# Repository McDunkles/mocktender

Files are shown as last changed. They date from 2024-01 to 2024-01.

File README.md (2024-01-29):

# L3-G8 Mocktail Mixing Machine Project

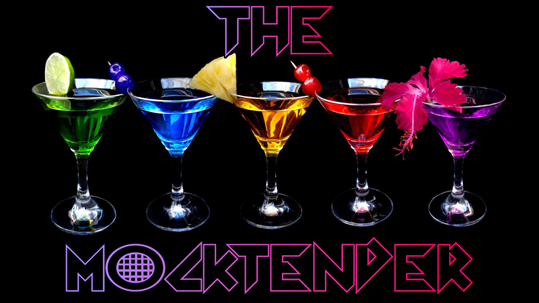
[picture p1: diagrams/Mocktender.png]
Mocktender Title Image


## Team Members:
The Mocktender was developped in Winter 2023 for the SYSC 3010 class by:
- Matt Reid
- Ethan Bradley
- Duncan MacLeod

#### TA: Roger Selzler

## About the Project
A mocktail is a non-alcoholic drink that captures the essence of a cocktail without the downsides of alcohol consumption. From work offices where you want to stay sharp while having fun drinks for lunch to wanting a healthier alternative to drinking cocktails at home. To provide the ease of having drinks at home or private events without needing to buy equipment and learn how to mix them yourself or paying a bartender, the Mocktender will provide the ability to create mocktails at home with ease. 

The Mocktender provides a web interface GUI that can be used to remotely view liquid levels, add recipes, change settings, and dispense drinks. Our project has three raspberry pi devices, one for the user interface, one for the machine (IOController), and one to simulate a second machine. The machine itself has a Raspberry Pi control device which is connected by GPIO to ultrasonic sensors to get the liquid level in real time. When a recipe is specified, it is sent through a Firebase real time database to the control device which runs peristaltic pumps to dispense the drink. An LCD displays output to the user of the machine showing the status of the machine.

## Contents
The contents of the top level directories are as follows:
- [/src](/src): Source code for the Mocktender including tests
- [/diagrams](/diagrams): Diagrams/Images used in Mocktender documentation and reports
- [/WIPUR](/WIPUR): Weekly Individual Projecet Update Reports
- [/3D_models](/3D_modles): 3D models for the liquid pump system (not used in final version)
- [/schematics](/schematics): Schematics used in Mocktender documentation and reports

The SRC (source code) folder contains the following directories:
- [/src/IOController](/src/IOController): Code for the IOController node which represents the real Mocktender machine
- [/src/SystemSimulator](/src/SystemSimulator): Code for the SystemSimulator node which simulates a Mocktender machine
- [/src/UserInterface/mkt-ui](/src/UserInterface/mkt-ui): Code for the UserInterface node which runs the Web Interface
- [/src/mkt-persistance](/src/mkt-persistane): Code for the persistance layer of the UserInterface node
- [/src/end2end](/src/end2end): Code and testing plan for the end to end test demonstration
- [/src/unittest](/src/unittest): Unit tests for the Mocktender machine. Includes the unit testing demo plan

## Installation
### Hardware

#### Electronics Necessary 
To build the hardware components of a Mocktender, the following components will be required:
- 1x Raspberry Pi 4B
- 3x UltraSonic Sensor
- 3x Peristaltic Pumps
- 2x L298N Dual H-Bridge driver
- 1x 1602A LCD Module
- 4x 220Ω resistor
- 3x 330Ω resistor
- 1x 2.2KΩ resistor
- 2x 9V rechargeable batteries

For documentation on how to connect these components together, please refer to Section 4 of the [Detailed Design Document](/documents/SYSC3010-TheMocktenderDetailedDesign-L3G8.pdf)

Food grade silicone hosing will also be required for pumping the liquid from the internal containers to a choice of reservoir.

### Software
#### Dependencies
A number of libraries need to be installed for a Mocktender to work.
The following commands can be used to install the necessary libraries (You may have to use `sudo` to install these properly):

```
python3 -m pip install pyrebase
python3 -m pip install gpiozero
python3 -m pip install adafruit-circuitpython-charlcd
```

#### Firebase Configuration
To begin getting the software all setup for a Mocktender, a Firebase Real-Time Database would need to be created for the user. The credentials for the project need to be filled out in [MocktenderConfig.py](/src/IOController/MocktenderConfig.py) as can be seen below:

```python
CONFIG_PROD = {
        "apiKey": "your-firebase-project-api-key",
        "authDomain": "your-firebase-project.firebaseapp.com",
        "databaseURL": "https://your-firebase-project-rtdb.firebaseio.com/",
        "storageBucket": "your-firebase-project.appspot.com"
}
```
In [dbFormat.json](/src/IOController/dbFormat.json), fill out the id value to be a name of your choosing.

```json
{
	"id": "device id name"
}
```
At the root of the project repo, the user should run the following commands

```bash
cd src/IOController/
python3 MocktenderRegistration.py production
```

This will upload the necessary schema to the Firebase Real-Time Database to run the Mocktender.

#### Email Notification Configuration 
The Mocktender also has email notification sending capabilities. To be able to use this functionality properly, please refer to [this repository](https://github.com/Brethan/ipy-mailer) for detailed instructions on how to set up an email for SMTP purposes.

In [notif_config.json](src/IOController/mailer/notif_config.json), use the values from the aforementioned instructions and paste them in this file.

```json
{
	"app_pw": "app-password",
	"sender": "your-python-smtp-email@gmail.com",
	"sender_name": "Mocktender"
}
```
## Usage
#### IOController Deployment
The IOController of the Mocktender can now be deployed by running the following commands at the root of the project directory:
```bash
cd src/IOController/
python3 IOLiquidLevel.py & python3 IOController.py production &
```

You should see IO device related errors due to IOLiquidLevel.py, followed by decimal numbers which are the 
measured liquid levels from the UltraSonic sensors. If one is paying attention to the Firebase RTDB,
they will noticed that there will be timestamped liquid levels being added to it.

Additionally, there will be errors from IOController.py due to issues with the asyncio API. The LCD screen
should say "Mocktender Ready" once it has been initialized.

The errors will not affect the runtime of the Mocktender.
## The Mocktender Machine
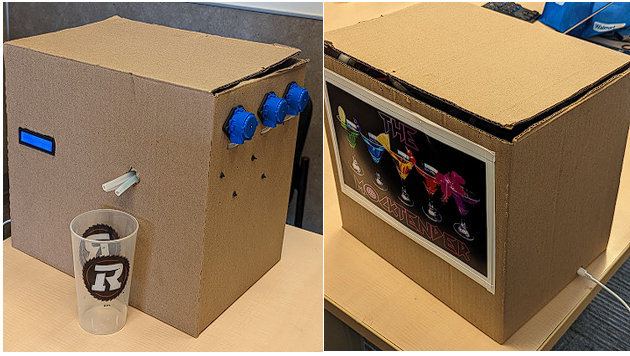
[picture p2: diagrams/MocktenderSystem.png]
Mocktender Machine


## UML Deployment Diagram

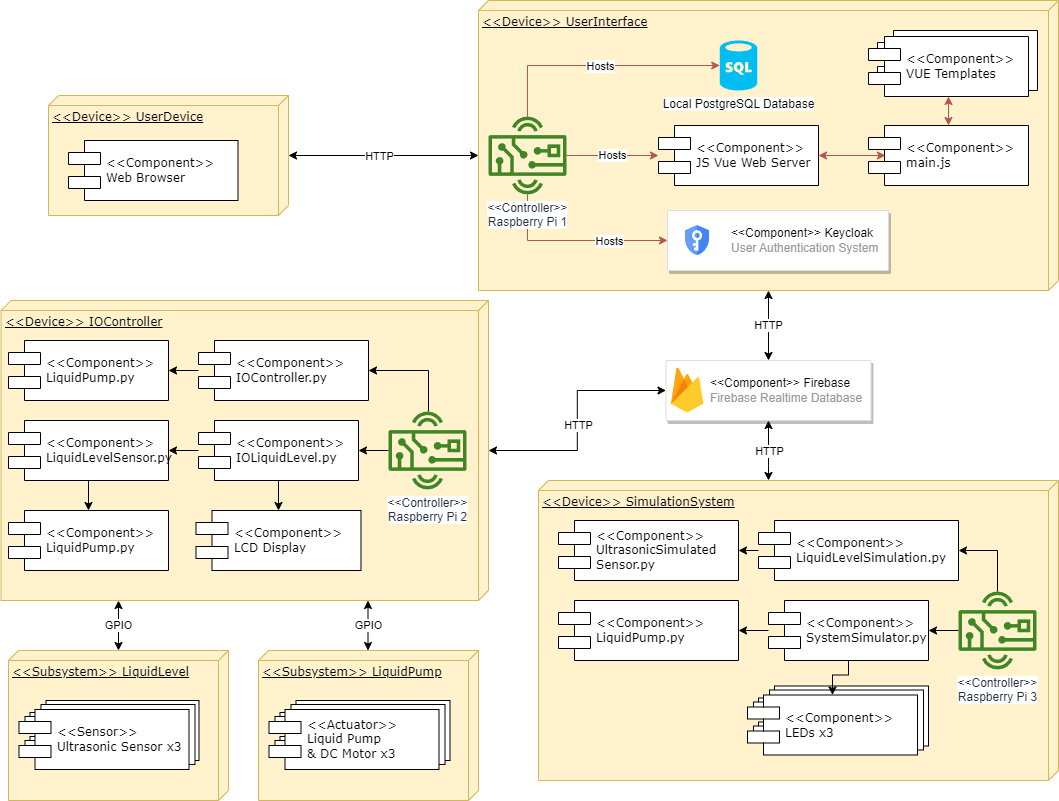
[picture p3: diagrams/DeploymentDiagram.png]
UML Deployment Diagram


## Project Milestones

| Milestone # | Name | Description |
| ---| -----| --- |
| 1 | Uploading and Fetching Data | Computer devices can read from and write data to a real-time database independently of each other, which can then be accessed and displayed on an external device. |
| 2 | Communication Between Nodes | Communication established between computer devices (HTTP etc.) to transfer data stored locally between nodes and issue commands. |
| 3 | Measurement and Conditional Actuation | Liquid level of a fixed container can be measured accurately using sensors can uploaded to the database. Data can be used to turn on an LED when a threshold is reached. |
| 4 | Exposing Data to the World | Two additional containers with liquid level measuring will also have their data uploaded to the database. The liquid level will be displayed as text on a webserver |
| 5 | Hardware Assembly | Assembled liquid dispensing system utilizing peristaltic pumps. Liquid level on webserver should be updated (as text) in real-time. |
| 6 | Graphical User Interface | Webserver displays the volume of the liquid containers as an animation. Users can navigate between different webpages on the server. |
| 7 | Controlling the Hardware System with UI | Webserver component can control all 3 liquid pumps implementing the drink mixing. Users can login and save customs mixtures locally and in the real-time database. |

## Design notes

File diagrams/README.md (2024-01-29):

# Mocktender Diagrams

Folder containing diagrams (deployment, class, and sequence) used for Mocktender documentation and reports

## Deployment Diagram
Deployment Diagram

## Sequence Diagrams
### CheckLiquidLevels Use Case
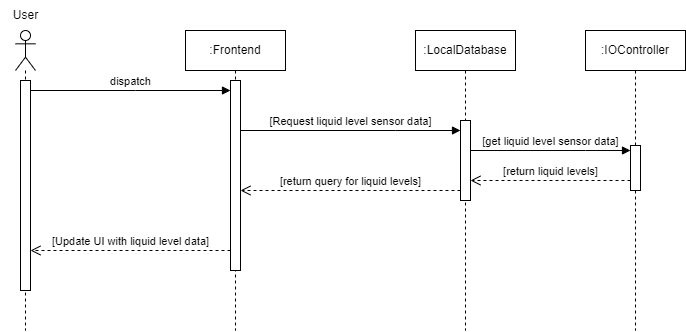
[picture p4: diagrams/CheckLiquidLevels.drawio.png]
CheckLiquidLevels


### MakeDrink Use Case
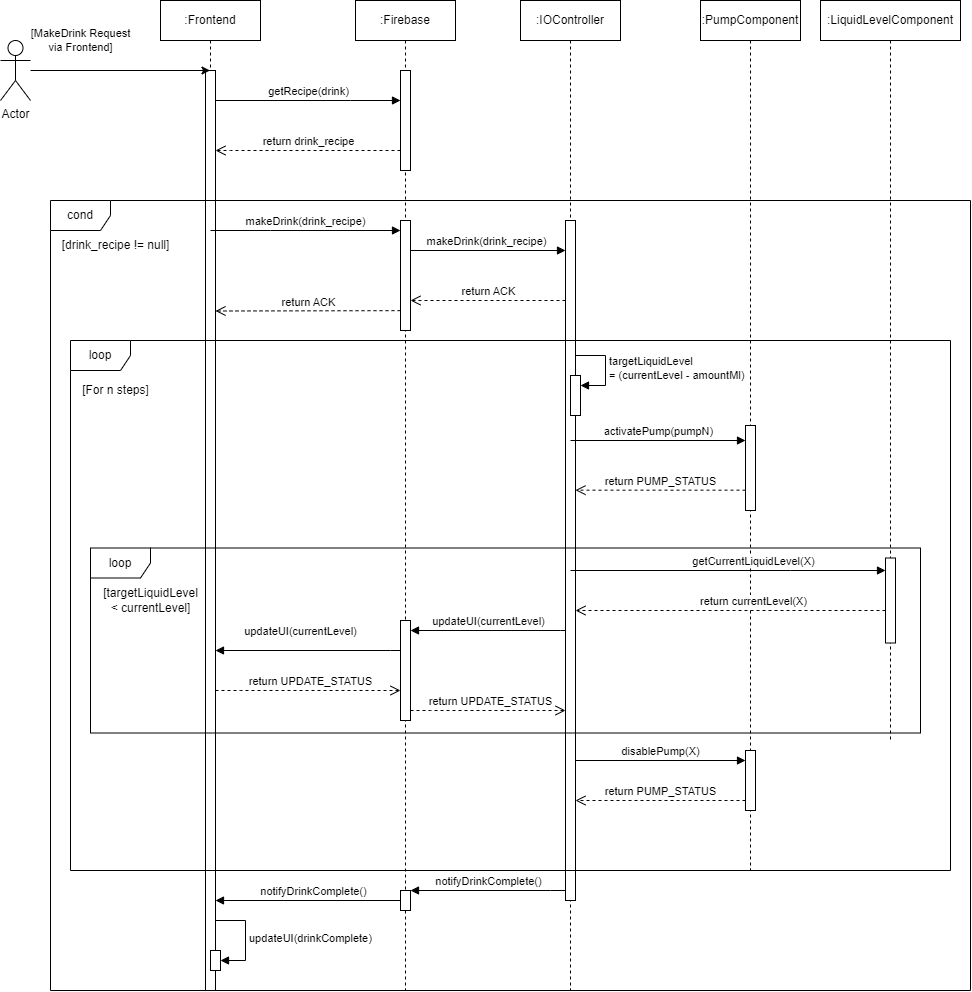
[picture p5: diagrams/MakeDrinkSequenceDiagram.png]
MakeDrink


## Class Diagrams
### IOController
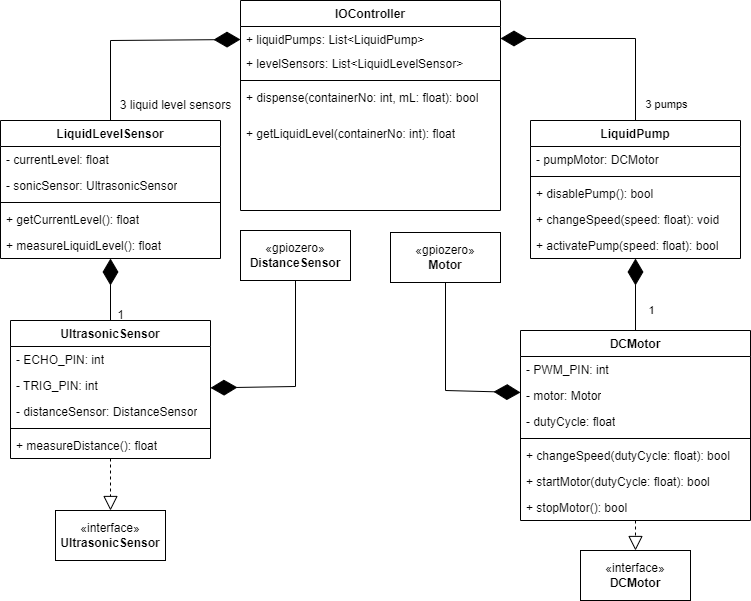
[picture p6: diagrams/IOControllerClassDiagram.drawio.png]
IOController


### IOSimulator
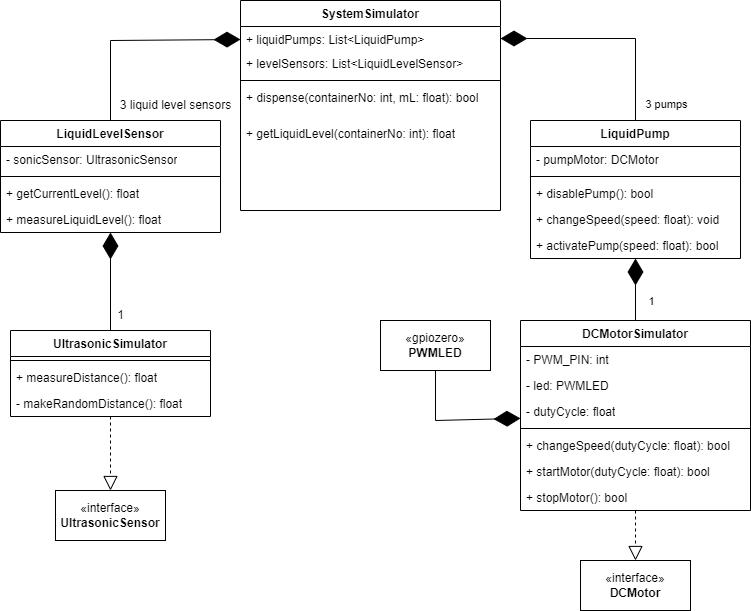
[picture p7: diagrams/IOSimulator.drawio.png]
IOSimulator


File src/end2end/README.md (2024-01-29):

# L3-G8 End-to-End Testing Demonstration
### Completed on March 10th, 2023

## Testing Plan
The Mocktender machine consists of multiple Raspberry Pi devices that need to communicate amongst each other to meet our project goals. The system is distributed between the Pi devices with one device hosting the front-end web interface for viewing the state of the machine and controlling the hardware devices. The User Interface device is responsible for updating the Firebase database with the liquid level sensor data and sending the signals to the hardware devices. The Sensor System and Simulation devices perform the same communication, so only one of them needs to be tested in end-to-end testing.
     To test the end-to-end communication between the components, all the messages discussed in Section 2.1 will need to be created. The test scripts created will generate the messages, send them to the correct end destination, and the end destination will confirm that the message was received, and the contents are as expected. The test will pass if the message is the same as was expected, and will fail if either no message was received, or the contents are different than was expected. To provide test feedback, the messages will be printed to a console that will also be available on the Raspberry Pi devices whenever needed as a debugging option. The database contents on the Firebase real time database will also be tested after the messages are sent to ensure that the contents are as expected.

The following steps will be performed in our end-to-end testing demonstration:
1. First, the connections between the Raspberry Pi devices, and the Firebase real time database will be tested. A test script will verify that all of the Pi devices are able to connect to the Firebase server.
2. Next, messages will be sent between Pi devices over the Firebase database to demonstrate that messages can be sent and received through that database.
3. Finally, a Flask web server will be created to demonstrate that a button press can send a message from the user interface pi to the Firebase database.

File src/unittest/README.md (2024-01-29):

# Mocktender Unit Testing Demo
### Group number: L3-G8

To test that each individual hardware and software component works as expected, the following hardware and software unit tests will be performed. A copy of the deployment diagram showcasing the system under test is below:
UML Deployment Diagram

## Hardware Unit Testing
| **Hardware Device** | **Tester** | **Device Description** | **Test Description** | **Expected Test** **Results** |
| --- | --- | --- | --- | --- |
| **Ultrasonic Sensor (Liquid level sensing)** | Matt | The ultrasonic sensor will be used to track the water level in the 3 liquid tanks in the Mocktender system. The distance from the sensor to the surface of the water is used to calculate the current volume of the liquid in the container. | To test the liquid level system is working correct, water will be added to the liquid container in increments of 2cm measured using a ruler. The Ultrasonic sensor will measure the distance to the surface of the water | The distance from the sensor to the surface of the water should  be within 5mm of the expected level based on the amount of water added to the container. |
| **Peristaltic Pump & DC Motor** | Ethan | The liquid pump will be used to dispense a drink. Based on the recipe provided by the user, each pump will be run for a specified amount of time so that the correct amount of each liquid is pumped (mixed) into the dispensed drink. | To test the functionality of the pump, the GPIO pin connected to the motor controller will be pulsed with PWM signals. The amount of liquid that is pumped over a time period will be measured. | The pump will pump water for 30 seconds in each trial, and approximately 50mL should be pumped into the measurement contzainer. |
| **LCD Display** | Duncan | The LCD display will display machine operation information such as what it is dispensing and any errors. | To test the LCD output, messages will be displayed on the LCD. | The LCD display should display the correct messages. |
| **Simulation LEDs** | Duncan | The simulation LEDs will light up when the motors on the simulation device are ON. Based on the recipe provided by the user, each LED will turn on for a specified amount of time so that it can be demonstrated that the simulation is working as expected. | To test that the Simulation LEDs accurately turn ON when the motors should be running, the LEDs will be pulsed with PWM similarly to the Peristaltic Pump & DC Motor test. This is since the simulation LEDs are simulating the pump and motor system | Like the pump and motor test, the user should see the LEDs gradually get brighter as the PWM is increased until they reach their max brightness. They will maintain the maximum brightness for 2 seconds before gradually slowing down until they are OFF. |

## Software Unit Testing
| **Software** | **Tester** | **Software Description** | **Test Description** | **Expected Test Results** |
| --- | --- | --- | --- | --- |
| **Liquid Level Monitoring System** | Matt | The liquid level monitoring system will take the sensor data and calculate the volume of liquid currently in the container in real time. It sends this information to the user interface to display to the user. | To test the conversion from distance to liquid level, increments of distances of 0.1 will be converted to a volume and rounded to the nearest volume amount in the software. There will also be tests for error values (negative and too high) | The volume that the software returns should be equal to the expected closest multiple of 80 to the distance. If the distance is negative or bigger than the maximum size (640mL), it should give a volume of -1. |
| **Motor Control System** | Ethan | The motor control system takes the amount of liquid needed for the selected recipe and converts it into the time that the motor needs to run based on the calculated flow rate. | To test that the motor control system can convert the recipe into the correct times for each pump to pump the specified amount of liquid. | The time that the system “turns on the motor” should match the expected time based on the recipe and flow rate. |
| **Frontend Web Interface** | Duncan | The frontend web interface allows a user to view liquid levels, create recipes, and dispense a drink. It also allows an admin login to give administrative access to locking a machine and | The interface will be tested by rendering GUI design pages and ensuring that they render and display information as expected. | When a button is pressed, it should redirect to the correct page and display the expected info. |
| **Local PostgreSQL Database** | Duncan | The local SQLite database is used to store machine specific data for display on the web interface. | The database will be tested using a test script which creates the expected tables for the local system database. | The data stored in the PostgreSQL database after the script is run will be pulled and compared with the expected contents of the database. |

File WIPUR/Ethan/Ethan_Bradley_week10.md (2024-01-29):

## Weekly Individual Project Update Report
### Group number: L3-G8
### Student name: Ethan Bradley (101158848)

### Week 10 (March 22nd - 28th)
___
1. **How many hours did you spend on the project this week?** 21

2. **Give rough breakdown of hours:**
   1. Writing technical memo: writing 1 hour
   2. Peristaltic Pump redesign + troubleshooting: CAD 12 hours
   3. Fixing the gearbox for the pump: CAD 5 hours
   4. Connecting gearbox, pump, and motor controller together: wiring 2 hours
   5. Met with team to discuss the video: meeting 1 hour
   6. Buying 3 peristaltic pumps from Amazon: resignation 0 hours

3. ***What did you accomplish this week?***
   - Lowered the scale of technical memo to just using a slicer.
   - Finished the integration of the pump with the gearbox.
   - Gave up on 3D printing the pump and gearbox.
   - Met with team to discuss the project video
  
4. ***How do you feel about your progress?***
   - Good progress this week. Feel deflated about the pumps, but I'm getting more sleep so that's nice.

5. ***What are you planning to do next week***? 
   1. Work on the project video for next weeks class.
   2. Get the Amazon pumps working with the liquid pump source code.
   3. Model mounting brackets for the pumps and funnel.

6. ***Is anything blocking you that you need from others?*** 
   - Nothing is blocking me right now.

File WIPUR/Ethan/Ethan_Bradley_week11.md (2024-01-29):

## Weekly Individual Project Update Report
### Group number: L3-G8
### Student name: Ethan Bradley (101158848)

### Week 11 (March 29th - April 4th)
___
1. **How many hours did you spend on the project this week?** 30

2. **Give rough breakdown of hours:**
   1. Integration of Frontend and IOController of the Mocktender: 11 hours
   2. Hardware assembly of the Mocktender Machine and wiring: 9 hours
   3. Recording for the final project video: 6 hours
   4. Editing the final project video: 4 hours

3. ***What did you accomplish this week?***
   - Integration between Frontend and IOController is complete (Frontend can actuate pumps)
   - IOController feedback loop is in progress (Pumps pump liquid, and use ultrasonic level sensors as a correction factor)
  
4. ***How do you feel about your progress?***
   - Significant progress made this week, not much left to go for the final demo

5. ***What are you planning to do next week***? 
   1. Clean up the communication between different systems clean up repo
   2. Mount funnel properly for final demo

6. ***Is anything blocking you that you need from others?*** 
   - Nothing is blocking me right now.

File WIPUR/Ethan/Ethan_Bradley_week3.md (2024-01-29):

## Weekly Individual Project Update Report
### Group number: L3-G8
### Student name: Ethan Bradley (101158848)

### Week 3 (January 25th - 31st)
___
1. **How many hours did you spend on the project this week?** 4

2. **Give rough breakdown of hours spent on 1-3 of the following:**
   1. Discussing project idea and implementation with group members, 2 hours
   2. Researching mechanisms for fluid transfer, 2 hours
3. ***What did you accomplish this week?***
  - Group decided on a Mocktail machine for our project
  - Progess made on the draft project proposal
  - Discussed the structure of the of the machine
4. ***How do you feel about your progress?***
  - I am personally a bit behind, but catching up
5. ***What are you planning to do next week***? 
  - Full project proposal 
  - Draft CAD drawing for a peristaltic pump
  - Discuss budget for items required for project
6. ***Is anything blocking you that you need from others?*** 
  - Nothing is currently blocking me

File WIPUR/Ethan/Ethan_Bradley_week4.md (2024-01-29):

## Weekly Individual Project Update Report
### Group number: L3-G8
### Student name: Ethan Bradley (101158848)

### Week 4 (February 1st - 7th)
___
1. **How many hours did you spend on the project this week?** 6

2. **Give rough breakdown of hours spent on 1-3 of the following:**
   1. Creating the circuit diagrams for the Draft proposal - 2 hours.
   2. Writing allocated section for draft proposal - 3 hours
   3. Discussion with group members about the various design and implementation details for the Mocktender - 1 hour
      1. Note: Some of these events over lap
3. ***What did you accomplish this week?***
  - Implementation for liquid transfer for the Mocktender was discussed, was decided to use gravity and valves instead of pumps.
  - Draft project proposal has been completed
    - By extension, decided on communication protocol between computer devices, as well as the sensors used for the project
4. ***How do you feel about your progress?***
  - I am still behind on labs, however should be done by Wednesday night.
5. ***What are you planning to do next week***? 
  - Polishing up the final project proposal based on the peer review for the draft.
  - Research valve designs that can utilize (servo) motors instead of typical metal valves
  - Figure out which components can be ordered on digikey and submit order form.
  - Start playing around with components I have on hand that relate to our project (LCD screen, ultrasonic sensor, etc.)
6. ***Is anything blocking you that you need from others?*** 
  - Need Duncan to assign an issue on GitHub for lab 4.

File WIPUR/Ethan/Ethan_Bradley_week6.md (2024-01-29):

## Weekly Individual Project Update Report
### Group number: L3-G8
### Student name: Ethan Bradley (101158848)

### Week 7 (February 22nd - 28th)
___
1. **How many hours did you spend on the project this week?** 6

2. **Give rough breakdown of hours:**
   1. Scouting out construction materials for the frame of the mocktender: 1.5 hours
   2. Began working on the detailed design document: writing 2.5 hours
   3. Researched PCB design technologies and how to use them: research 2 hours

3. ***What did you accomplish this week?***
   - Group began work on the detailed design document
   - Contacted SCE services to book an appointment for soldering training.
  
4. ***How do you feel about your progress?***
   - A bit worried, we were hoping to get more done during reading week but we were not really able to find any time to work on the project specifically.

5. ***What are you planning to do next week***? 
   1. Need to get everything necessary prepared to work on the detailed design document.
   2. Getting training from SCE services to be able to use the soldering iron in the maker lab.
   3. Find suitable and affordable chassis for the Mocktender.

6. ***Is anything blocking you that you need from others?*** 
   - Nothing is blocking me right now.

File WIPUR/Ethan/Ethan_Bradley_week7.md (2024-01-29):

## Weekly Individual Project Update Report
### Group number: L3-G8
### Student name: Ethan Bradley (101158848)

### Week 7 (March 1st - 7th)
___
1. **How many hours did you spend on the project this week?** 6

2. **Give rough breakdown of hours:**
   1. Purchased a hose and ball bearings for the peristaltic pumps: shopping 1 hour
   2. Progress made on detailed design document: writing 2 hours
   3. Got Maker Lab soldering training: training 1 hours
   4. CAD design drawings for peristaltic pumps: design 2 hours

3. ***What did you accomplish this week?***
   - Group worked on the detailed design document.
   - Learned how to use the soldering equipment in the Maker lab.
   - Purchased materials for the Mocktender, as well as modified some 3D models of peristaltic pumps on the internet
  
4. ***How do you feel about your progress?***
   - We are behind on the End to End testing, hoping to get it done Wednesday night.

5. ***What are you planning to do next week***? 
   1. Clean up detailed design document for the final submission.
   2. 3D print first prototypes for the peristaltic pump chassis.
   3. Begin work on unit tests for the unit test demo.
   4. Wrap up work on the End to End testing for the demo.

6. ***Is anything blocking you that you need from others?*** 
   - Nothing is blocking me right now.

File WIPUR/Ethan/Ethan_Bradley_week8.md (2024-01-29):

## Weekly Individual Project Update Report
### Group number: L3-G8
### Student name: Ethan Bradley (101158848)

### Week 8 (March 8th - 14th)
___
1. **How many hours did you spend on the project this week?** 8

2. **Give rough breakdown of hours:**
   1. Wrapping up the detailed design document: writing 4 hours
   2. Peristaltic pump prototyping: R&D 3 hours
   3. Writing software for inter-node communication: software 1 hour

3. ***What did you accomplish this week?***
   - Group wrapped up work on the detailed design document, working on finishing touches up to Wednesday.
   - Printing and test fitting the peristaltic pump designs, making necessary modifications to reduce friction.
   - Writing the software necessary to have the nodes communicate properly.
  
4. ***How do you feel about your progress?***
   - We are in the process of catching up to our projected milestone deadlines, however some extra elbow grease is in order.

5. ***What are you planning to do next week***? 
   1. Pick a topic to write about for the technical memo.
   2. Integrate pump housing with motors to have a functional liquid pump.
   3. Begin work on software related unit testing for the unit testing demo.
   4. Extra communication backbone development to make up for our poorly prepared E2E demo.
   5. Experiment with lubricants for the peristaltic pump housing.

6. ***Is anything blocking you that you need from others?*** 
   - Nothing is blocking me right now.

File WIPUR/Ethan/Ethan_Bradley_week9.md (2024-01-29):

## Weekly Individual Project Update Report
### Group number: L3-G8
### Student name: Ethan Bradley (101158848)

### Week 9 (March 15th - 21st)
___
1. **How many hours did you spend on the project this week?** 15

2. **Give rough breakdown of hours:**
   1. Writing technical memo draft: writing 2 hours
   2. Peristaltic Pump redesign + troubleshooting: CAD 8 hours
   3. Designing a gearbox for the pump: CAD 3 hours
   4. Unit test demo preparation (source code): programming 2 hours

3. ***What did you accomplish this week?***
   - Picked a topic for the technical memo (CAD and 3D printing) and started writing a script for the video
   - Had to completely redesign the pump model I was using due to it not playing well with the size of the bearings we bought.
   - Printed a gearbox due to the RPM of our motors being too high to do anything useful.
   - Prepared unit tests for the unit test demo so that they're ready to go when the pumps are complete.
  
4. ***How do you feel about your progress?***
   - We're steadily catching up to our milestone deadlines. The mechanical issues with the pump are a bit discouraging.
   I believe this is what's referred to as "integration hell".

5. ***What are you planning to do next week***? 
   1. Completing the technical memo using feedback from the peer review.
   2. Fix up all of the issues with the pumps.
   3. Wrap up working on the unit test demo, hopefully by Thursday.

6. ***Is anything blocking you that you need from others?*** 
   - Nothing is blocking me right now.

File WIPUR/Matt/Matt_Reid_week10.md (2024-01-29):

## Weekly Individual Project Update Report
### Group number: L3-G8
### Student name: Matt Reid (101140593)

### Week 10 (March 22nd - 28th)
___
1. **How many hours did you spend on the project this week?** 12 hours

2. **Give rough breakdown of hours:**
   1. Worked on creating lid for the liquid container that can hold ultrasonic sensor: deisgn 2 hours
   2. Finalized the unit test for the hardware of the ultrasonic sensor: development/testing 2 hours
   4. Updated unit testing plan with up to date test information: writing 1 hour
   4. Connected all 3 ultrasonic sensors to the pi at once and used the hardware test on each: development/testing 2 hours
   6. Finzlized software unit test for the ultrasonic sensor adding pytest for automation: development 4 hours
   7. Met with team to plan making our video and finishing the project: meeting 1 hour

3. ***What did you accomplish this week?***
   - We demonstrated our unit testing.
   - I finished and demonstrated my hardware and software unit tests for the unit testing demo.
   - I added in the other ultrasonic sensors and started coding the complete system.
  
4. ***How do you feel about your progress?***
   - I feel like our progress this past week was good, we were a bit behind on the database at the unit test demo.

5. ***What are you planning to do next week***? 
   1. Meet with team to work on implementing the entire system as one (adding pumps, ultrasonic sensors and LCD to one IOController node).
   2. Continue work on coding the complete device with ultrasonic messages from all 3 sensors sent to the UI.
   3. Create our project video with the team to present in class next Wednesday.
   4. Work towards starting the final report.

6. ***Is anything blocking you that you need from others?*** 
   - Nothing is blocking me right now.

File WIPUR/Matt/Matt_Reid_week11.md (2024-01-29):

## Weekly Individual Project Update Report
### Group number: L3-G8
### Student name: Matt Reid (101140593)

### Week 11 (March 29th - April 4th)
___
1. **How many hours did you spend on the project this week?** 20 hours

2. **Give rough breakdown of hours:**
   1. Created lids for the other two liquid containers and mounted them in the frame: construction 1 hour
   2. Performed testing on the accuracy of the distance to volume convesions of all 3 sensors at once: testing 2 hours
   4. Started work on organizing the github and creating READMEs for final submission: docs/organization 1 hour
   4. Worked on creating slides and script for final project video: writing 3 hours
   6. Connected the LCD to the system frame and ensured messages are sent as desired: construction/testing 2 hours
   7. Added functionality to get the median of 10 volume measurements to improve accuracy: development 1 hour
   8. Worked to iron out bugs in the ultrasonic code and add minor features: development/testing 4 hours
   9. Met with team to integrate the entire system into the frame and plan last steps: meeting/construction 6 hours

3. ***What did you accomplish this week?***
   - We created our final project video
   - I completed the ultrasonic liquid level system (all that is left is testing and fine tuning)
   - The mocktender is able to dispense recipes from the user interface. The system is fully integrated. For my part, the liquid
     levels are successfully sent in real time and displayed to the user via the user interface liquid level page.
  
4. ***How do you feel about your progress?***
   - I feel like our progress this past week was amazing, we are fully on track to have a complete working system next Wednesday.

5. ***What are you planning to do next week***? 
   1. Meet with team to make final touches to the machine construction
   2. Perform rigorous integration testing on the system.
   3. Prepare for the final demonstration and github review.
   4. Work on the final project report.

6. ***Is anything blocking you that you need from others?*** 
   - Nothing is blocking me right now.

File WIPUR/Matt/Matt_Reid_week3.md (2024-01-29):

## Weekly Individual Project Update Report
### Group number: L3-G8
### Student name: Matt Reid (101140593)

### Week 3 (January 25th - 31st)
___
1. **How many hours did you spend on the project this week?** 5

2. **Give rough breakdown of hours spent on 1-3 of the following:**
   1. Determining project idea and scope: brainstorming/evaluating options, 3 hours
   2. Resarching state of the art and building materials: research, 2 hours
3. ***What did you accomplish this week?***
  - Decided on a mocktail machine as our project idea
  - Started resarching component costs and buidling materials
  - Worked on draft project proposal for peer review
4. ***How do you feel about your progress?***
  - Good progress
5. ***What are you planning to do next week***? 
  - Work on creating full project proposal for peer review
  - Create list of parts and where to order them from
  - Create solid plan for meeting all of the project criteria
6. ***Is anything blocking you that you need from others?*** 
  - Nothing is currently blocking me

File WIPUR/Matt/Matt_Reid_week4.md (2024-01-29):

## Weekly Individual Project Update Report
### Group number: L3-G8
### Student name: Matt Reid (101140593)

### Week 4 (February 1st - 7th)
___
1. **How many hours did you spend on the project this week?** 10

2. **Breakdown of hours spent:**
   1. Determining project components: brainstorming/evaluating options, 3 hours
   2. Resarching statistics and state of the art for proposal: research, 1 hours
   3. Working on the project proposal: writing, 6 hours

3. ***What did you accomplish this week?***
  - Decided on a ultrasonic sensor to measure water level
  - Worked on project proposal for peer review
  - Created rough plan of project design

4. ***How do you feel about your progress?***
  - Good progress

5. ***What are you planning to do next week***? 
  - Work on updating proposal with peer review feedback
  - Start getting parts together so building can commence in reading week

6. ***Is anything blocking you that you need from others?*** 
  - Nothing is currently blocking me

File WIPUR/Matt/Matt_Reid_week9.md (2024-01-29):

## Weekly Individual Project Update Report
### Group number: L3-G8
### Student name: Matt Reid (101140593)

### Week 9 (March 15th - 21st)
___
1. **How many hours did you spend on the project this week?** 10 hours

2. **Give rough breakdown of hours:**
   1. Worked on final edits to the detailed design document for submission: review/editing 1 hour
   2. Created a unit test for the hardware of the ultrasonic sensor and tested the results: development/testing 3 hours
   3. Reasearch connecting the LCD to the Pi and how to fix contrast problem: research 1 hour
   4. Updated unit testing documentation to reflect most up to date testing plans: writing 1 hour
   4. Created LCD hardware unit test and ensured it functions as expected: development/testing 2 hours
   6. Started work of software testing for the Ultrasonic Sensor. Took measurements and created table: development 2 hours

3. ***What did you accomplish this week?***
   - I submitted our detailed design docuemnt
   - I created my hardware and software unit tests for the unit testing demo.
   - I tested the hardware and software units (Ultrasonic and LCD) to ensure they are working as expected.
  
4. ***How do you feel about your progress?***
   - I feel like our progress this past week was good, and we should do well at the unit testing demo.

5. ***What are you planning to do next week***? 
   1. Finish implementing software unit test for the Ultrasonic Sensor.
   2. Continue work on completing project milestones as scheduled.
   3. Meet with the team to confirm that we are on track for the unit testing demo.
   4. Complete the unit testing demo on Friday.

6. ***Is anything blocking you that you need from others?*** 
   - Nothing is blocking me right now.

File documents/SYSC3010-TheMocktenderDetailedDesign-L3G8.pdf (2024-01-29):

# SYSC3010 | Computer Systems Development Project

# Detailed Design

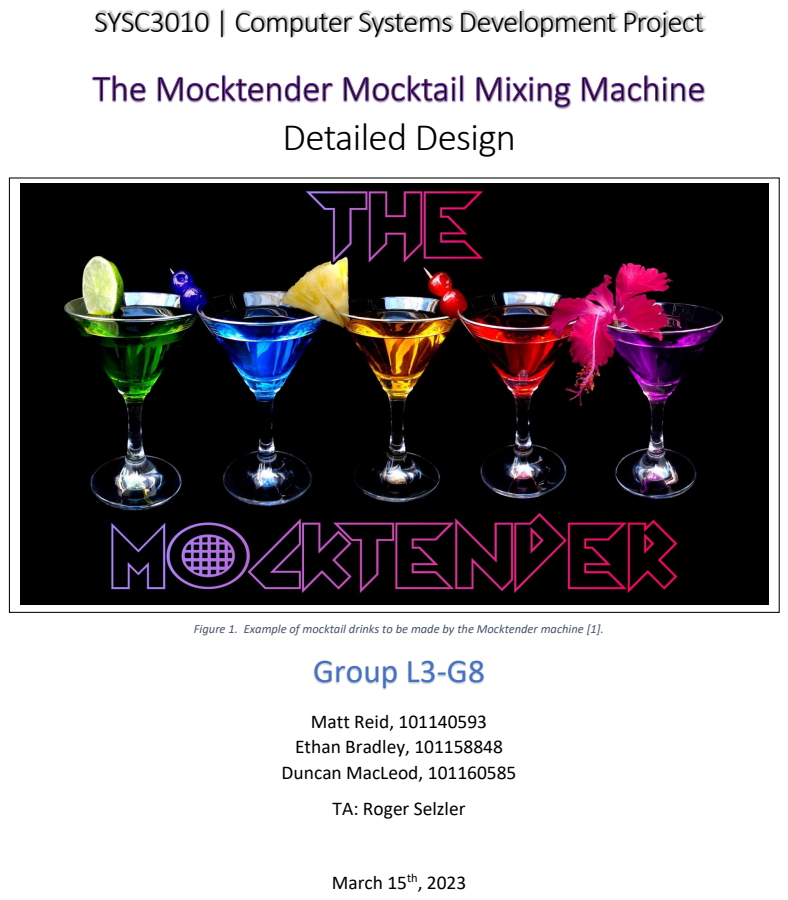
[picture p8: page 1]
Group L3-G8; March 15th, 2023

Figure 1. Example of mocktail drinks to be made by the Mocktender machine [1].

Matt Reid, 101140593
Ethan Bradley, 101158848
Duncan MacLeod, 101160585
TA: Roger Selzler

THE MOCKTENDER MOCKTAIL MIXING MACHINE - DETAILED DESIGN

## Table of Contents

## 1 Problem Statement

A mocktail is a non-alcoholic drink that captures the essence of a cocktail without the downsides of alcohol consumption. From work offices where you want to stay sharp while having fun drinks for lunch to wanting a healthier alternative to drinking cocktails at home, there are lots of reasons to enjoy a mocktail. As more people look towards health and wellness trends, the number of people drinking non-alcoholic beverages is rapidly increasing. A NielsenIQ study in October 2021 found that non-alcoholic beverage sales had gone up 33.2% in 12 months to a total market of $331 million [2]. In the United States, 30% of people who are of drinking age do not drink alcohol [3], and according to a 2021 survey by Statistics Canada, 1 in 5 Canadians said they have been drinking less than before the COVID-19 pandemic [4].

The objective of the project is to create an automated mocktail mixing machine that provides a web interface to allow dispensing drinks, administrative access, real-time liquid level monitoring, and recipe creation. It replaces the need for at home mixing equipment, and bartenders at events to eliminate the inflated cost of making mixed drinks. It will provide timely mocktails from specified recipes, allowing for easy access to mocktails and less time spent mixing with more time spent drinking.

### 1.1 Functional Requirements

To create an easy to use and fully functional mocktail mixing machine, The Mocktender will meet the following functional requirements:

Automatic Liquid Mixing: The machine will automatically mix liquids together based on defined recipes in a database. The database will contain recipes that specify liquid percentages, and the Raspberry pi will use a pump to dispense the correct amount of each liquid into a cup.

Administrative Access: The machine will allow an admin user to login to the web interface and lock the machine from use or modify the liquid types that are available in the machine. Admin users can also control who has access to the machine.

Remote Dispensing Access: The machine will allow users to access the drink pouring menu remotely on a web interface. GUI (Graphical User Interface) buttons will be available to dispense selected drink recipes from a list.

Recipe Creation and Storage: The machine will allow users to create new recipes in a web interface and store them in a database. Recipes consist of liquid names and the percentage of each liquid that should be pumped into the cup.

Remote Liquid Level Monitoring: The machine will allow users to view the current liquid levels through a web interface page. An ultrasonic sensor will be used to provide real-time updates of the liquid levels. Notifications will be sent to registered users that liquid levels are low.

## 2 Design Overview

### 2.1 System Overview Diagram

The Mocktender System consists of a Raspberry Pi device which provides a user interface (UserInterface node) that is connected to one or more Raspberry pi devices which represent I/O controllers (IOController/SimulationSystem nodes) of a Mocktender system. In our project, we use one Raspberry Pi device to act as a physical Mocktender IOController as well as a SimulationSystem Pi device which simulates the behaviour of a Mocktender device to showcase that more than one device can be utilized at once (scalability). The UserInterface device and the IOController/SystemSimulator devices communicate over HTTP using a Firebase Realtime Database which stores data (messages) sent between the devices. These messages include requests for real-time liquid levels and instructions for the pumps to dispense a desired recipe. The Flask webserver hosted by the UserInterface Pi device is accessed by a user’s web browser over HTTP, providing the GUI for the system. This deployment diagram is shown in Figure 2 below.

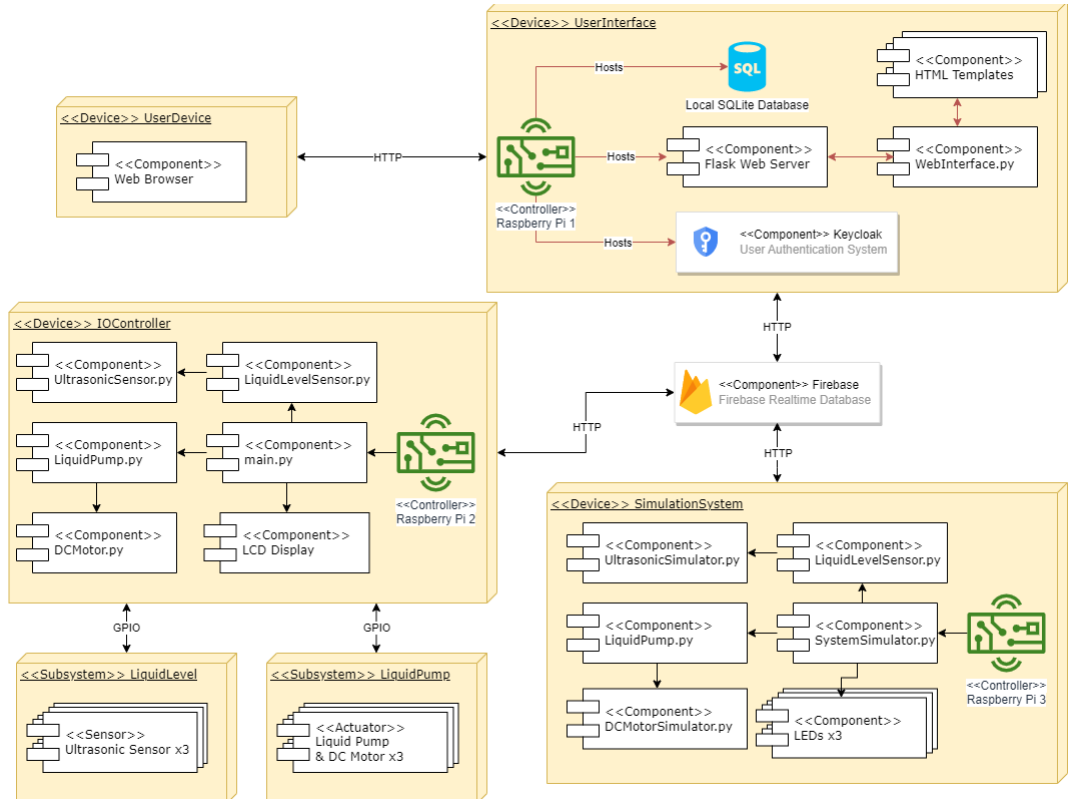
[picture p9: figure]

Figure 2. Deployment diagram of The Mocktender Mocktail Mixing Machine.

As discussed above, there are three device systems which are controlled by a different Raspberry Pi. The first Raspberry Pi controls the “UserInterface” node, and hosts the local Flask based web interface as well as the SQLite database and Keycloak server to provide local data storage and user authentication. The web interface provides the user with access to the Mocktender system and connects to the Firebase Realtime Database to send instructions to the LiquidPump subsystem and receive liquid level data from the LiquidLevel subsystem. More information about the functionality of the Flask web interface can be found in Section 5 (GUI Design). The second Raspberry Pi in our project controls the “IOController” node and is connected over GPIO to the LiquidLevel and LiquidPump subsystems which contain physical Ultrasonic Sensors, and Liquid Pump actuators. The device runs a Python script which controls getting the real-time liquid level and sending instructions to the liquid pumps. It also has an LCD display which provides output to the user that is getting a drink from the machine. Additional information about the software systems can be found in Section 3, and the hardware systems can be found in Section 4. The internal systems that make up the IOController, including the Liquid Pump Subsystem and the Liquid Level Subsystem can be seen below in Figure 3.

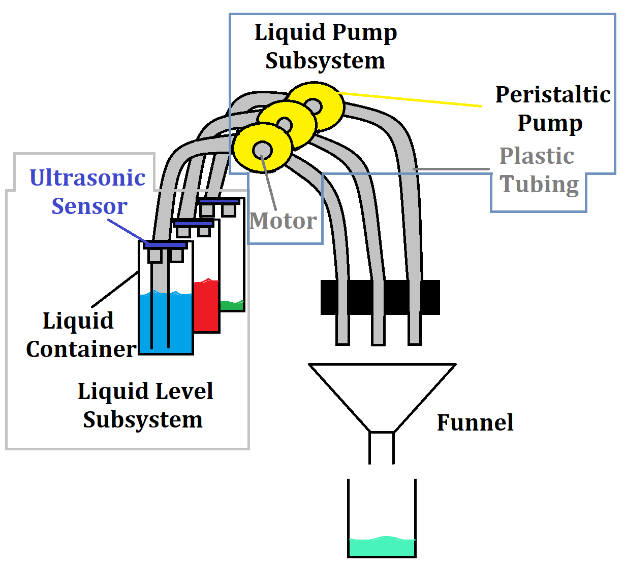
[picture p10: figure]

Figure 3. Sketch of internal Mocktender systems.

The third Raspberry Pi controls the “SimulationSystem” node, which simulates the functionality of the IOController. Like the IOController, it provides liquid level data and takes liquid pump instructions, however instead of using physical Ultrasonic Sensors, and Liquid Pumps, they are simulated in software. Instead of an LCD device providing output, the simulation provides output in a terminal simulating what would go on the LCD device. The SimulationSystem also has three LEDs which simulate the pumps and light up when the pumps are being run to show that the instructions are being receive and processed correctly. The SystemSimulator both showcases that the system can work with more than one device, and that the software works independent of the physical hardware sensors and actuators.

### 2.2 Communication Protocols

There are two different communication types used by the Mocktender system, HTTP connections for the Firebase Realtime Database, and GPIO connections for the hardware sensors and actuators.

The liquid level sensors can be controlled using GPIO as they operate using digital signals. Similarly, the pump controllers can be controlled using GPIO. As we are implementing the pumps with DC motors, we will their speed using a PWM GPIO signal so that the liquid flow rate can be more accurately controlled. The Liquid Level system will be on a periodic timing loop and will provide the script in the UserInterface with the current liquid level in real-time.

Each Raspberry Pi node will upload to and read from the Firebase Realtime Database. The Firebase database will be used to both store data necessary for the operation of the Mocktender as well as to provide a platform for the Raspberry Pi nodes to issue and receive commands. The Raspberry Pi nodes will communicate with the Firebase database using HTTP. Section 2.2.1 below shows the various message types and data formats that will be sent between nodes via the Firebase Realtime Database.

2.2.1 Communication Protocol Tables
The internode communication between the UserInterface, IOController, and SimulationSystem through the Firebase Realtime Database, and the LiquidPump subsystem are outlined in the communication protocol tables in the following sections.

2.2.1.1 User Interface
The User Interface communicates with every node of the system. It primarily communicates with the Firebase Database to read the Liquid Level of a Mocktender Machine, fetch a recipe, change the liquid names, and adding users to a Mocktender. A route to control the IOController has also been left exposed so that the user is able to send commands to the hardware devices to make drinks using the Frontend Web Interface. The messages received by and sent from the UserInterface can be seen below in Table 2.2.1.1.

Table 2.2.1.1 Communication Protocol Table for the UserInterface node.

Sender | Receiver | Message | Request | Data Format
User Interface | Firebase | getLiquidLevel | GET | Request: JSON { "subject": "liquid-level", "deviceId": INTEGER, "containerNo": INTEGER } Response: JSON { “liquidLevel”: NUMBER, }
User Interface | Firebase | getRecipe | GET | Request: JSON: {

| | | | “subject”: “recipes”, “deviceId”: INTEGER, “drink”: STRING } Response: JSON { “recipe”: STRING }
User Interface | Firebase | changeLiquid | PUT | Request: JSON { “deviceId”: INTEGER, "containerNo": INTEGER, "liquid": "newLiquid" } Response: JSON { “containerNo”: INTEGER, “liquid”: “newLiquid” }

User
Interface
IOController | makeDrink | POST | Request: JSON { “deviceId”: INTEGER, “drinkId”: INTEGER, “recipe”: STRING }
| | | Responses: JSON (updateUI) { “deviceId”: INTEGER, “containerNo”: INTEGER, “liquidLevel”: NUMBER }
| | | JSON (notifyDrinkComplete) { “deviceId”: INTEGER, “drinkId”: INTEGER, “status”: BOOLEAN }

User
Interface
WebServer | login | POST | Request: JSON { “subject”: “login”, “username”: STRING, “password”: STRING

| | | | }
User Interface | WebServer | addUser | PUT | Request: JSON { “subject”: “addUser”, “deviceId”: INTEGER, “username”: STRING, “password”: STRING } Response: JSON (reject) { “deviceId”: INTEGER, “reason”: STRING }
User Interface | Firebase | subscribe | PUT | Request JSON { “subject”: “subscribe”, “deviceId”: INTEGER, “username”: STRING, “email”: STRING }
User Interface | Firebase | unsubscribe | DELETE | Request JSON { “subject”: “unsubscribe”, “deviceId”: INTEGER, “username”: STRING, “email”: STRING }

2.2.1.2 IOController and SimulationSystem
The IOController’s communication is responsible for periodically updating the liquid level of the Mocktender’s liquids on the Firebase Real-time database. It is also responsible for communicating with the Frontend of the UserInterface to update the liquid level values in real time. The SimulationSystem node is designed to replicate the IOController and will send the same messages as the IOController. Table 2.2.1.2 below shows the messages sent from the IOController/SimulationSystem to the other nodes of the system.

Table 2.2.1.2 Communication Protocol Table for the IOController and SimulationSystem node.

Sender | Receiver | Message | Request | Data Format
IOController/ SimulationSystem | Firebase | updateLiquidLevel | PUT | Request: JSON { “subject”: “liquid-level”, “deviceId”: INTEGER, “containerNo”: INTEGER, “liquidLevel”: NUMBER }
IOController/ SimulationSystem | User Interface | updateUI | PUT | Requests: JSON (updateLiquidLevel) { “subject”: “currentLevel”, “deviceId”: INTEGER, “containerNo”: INTEGER, “liquidLevel”: NUMBER } JSON (updateDrinkStatus) { “subject”: “drinkComplete", “deviceId”: INTEGER, “drinkStatus”: BOOLEAN, }
IOController/ SimulationSystem | User Interface | notifyLowLiquid | POST | Requests: JSON { “subject”: “lowLiquid”, “deviceId”: INTEGER, “containerNo”: INTEGER, “liquidLevel”: NUMBER }

2.2.1.3 Liquid Pump Subsystem
The liquid pump system is controlled by the UserInterface using the IOController as a proxy. It is responsible for listening the commands from the UserInterface to turn a pump on or off for a specified container. Table 2.2.1.3 below shows the commands that the liquid pump system will listen for.

Table 2.2.1.3 Communication Protocol Table for the LiquidPump.

Sender | Receiver | Message | Data Format
UserInterface | IOController::LiquidPump | activatePump | JSON { “subject”: “liquidPump”, “deviceId”: INTEGER, “containerNo”: INTEGER, “pumpState”: True }
UserInterface | IOController::LiquidPump | disablePump | JSON { “subject”: “liquidPump”, “deviceId”: INTEGER, “containerNo”: INTEGER, “pumpState”: False }

### 2.3 Message Sequence Diagrams

2.3.1 Message Sequence Diagram 1: MakeDrink Use Case
The most basic use case demonstrating the process to make a drink is the MakeDrink use case, which is done through the local web interface. The sequence diagram below in Figure 4 demonstrates the use case of making a drink using the web interface. The user will connect to the Frontend Flask web server using HTTP from their web browser. The Mocktender web interface will display all saved Mocktails that are currently available based on the liquids in the machine. The user will be able to select the drink they want to make. When the user confirms their choice, the SystemInterface will pour the drink by communicating with IOController, signalling which pumps to start and stop. When the drink is done, the UI will update indicating that the drink has been poured.

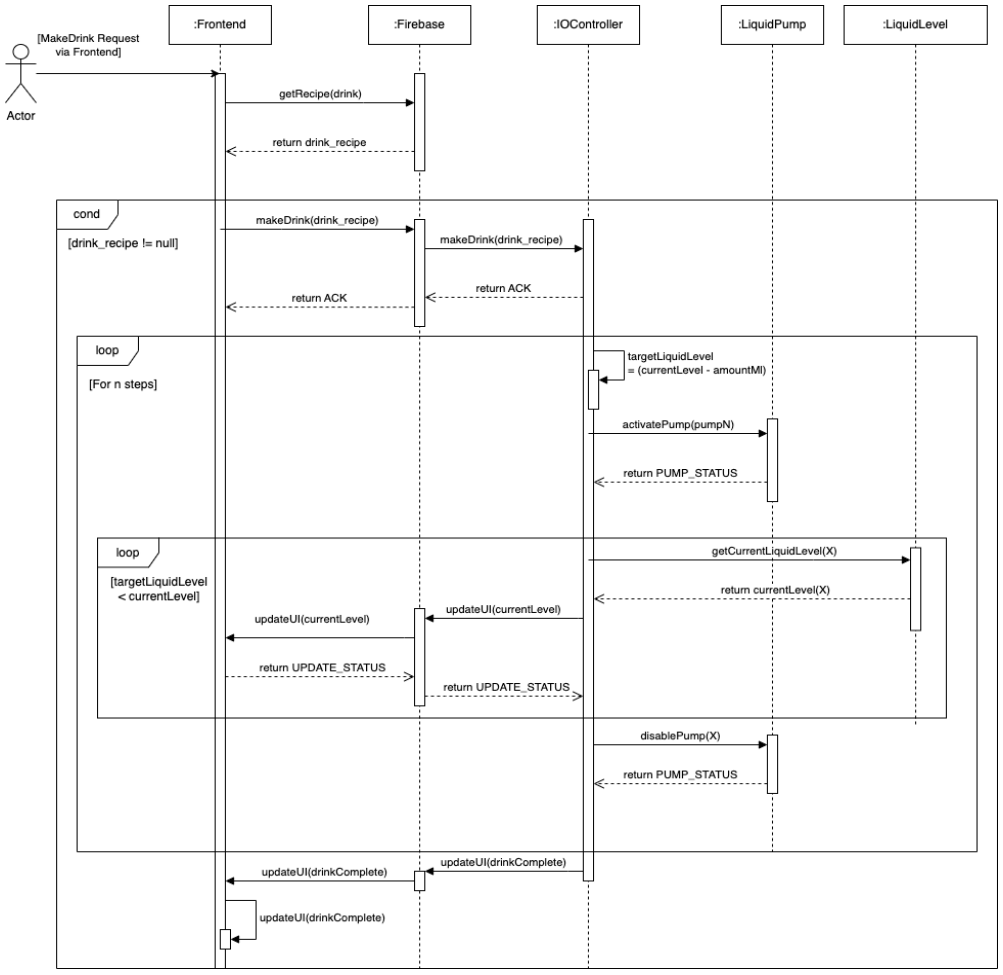
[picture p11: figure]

Figure 4. Sequence diagram for use case 1: MakeDrink.

2.3.2 Message Sequence Diagram 2: CheckLiquidLevels Use Case
The Mocktender is equipped with sensors to track how much liquid is left in each container, which the user can view through the web interface. The CheckLiquidLevels use case outlines the process of checking the current liquid levels as a user of the system. As in the previous use case, the user is connected to the Frontend Flask web server using HTTP from their web browser. Viewing the liquid levels can be completed by pressing a button on the UI, which will make a call to the local database to fetch the current liquid levels and display them to the user (See Section 5 for GUI design). After the button is pressed, the Flask Web Server sends a message to the local SQLite database to request the most recent liquid level sensor data. The SQLite database returns the result of the query, and it is displayed to the user on the web interface (LocalUI). The sequence diagram showcasing the process of checking a liquid level can be seen below in Figure 5.


Figure 5. Sequence diagram for use case 2: CheckLiquidLevels.

2.3.3 Message Sequence Diagram 3: CreateNewRecipe Use Case
The MakeRecipe use case outlines the basic flow of the process to create a new mocktail recipe, which is done through the web interface. As in the other use cases, the user is connected to the web interface (LocalUI) through HTTP from their web browser. Figure 6 shows the process of interacting through the web interface to create a recipe. The user navigates through the web interface by going to “Settings” ->” Update UI” ->” View/Edit Saved Recipes.” From there, the user will be able to specify a sequence of drinks to pour to create their new mocktail. Once saved, the new mocktail is now available to make.

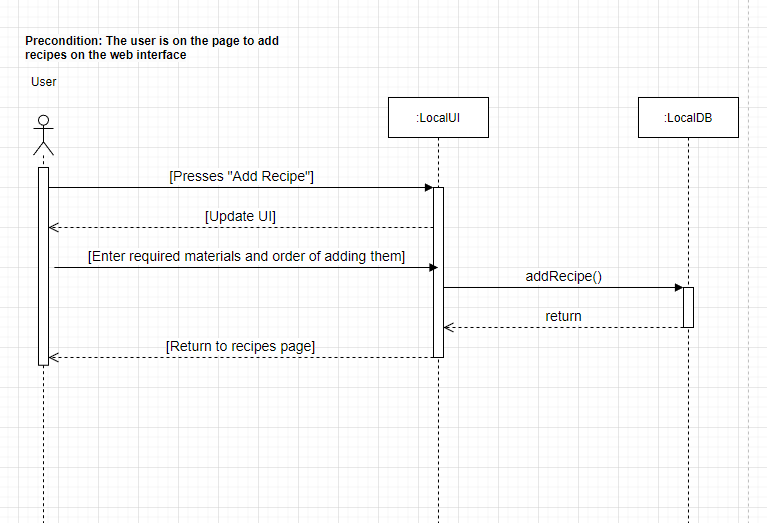
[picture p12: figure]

Figure 6. Sequence diagram for use case 3: CreateNewRecipe.

### 2.4 Database Table Design/Schema

The Mocktender will have both a local SQLite database and a cloud Firebase Realtime Database. The SQLite database is hosted on the UserInterface Pi device, and each instance is specific to each Mocktender machine (each IOController/SystemSimulation node). The information that is received from the IOController and SystemSimulation nodes through the cloud Firebase Database are stored in the local database to be retrieve by the frontend web server for display to the user. As shown above in section 2.2, the cloud Firebase Realtime Database is used to send messages between the nodes of the system containing liquid level and recipe information. Figure 7 below shows the machine-specific database schema which is merged between both database types. The database schema can be split into two categories, which are colour coded in red and purple. Database tables in red store data that is primarily used for the Mocktender’s main function, creating mixed drinks. Database tables in purple and the Keycloak table are related to user information and authentication. The machine-specific database stores liquid level info saved mocktail recipes, the liquids that are in the containers, and data on whether the recipe can be created with the current liquid levels. It also stores the user information and user types which are used by the Keycloak user authentication service.

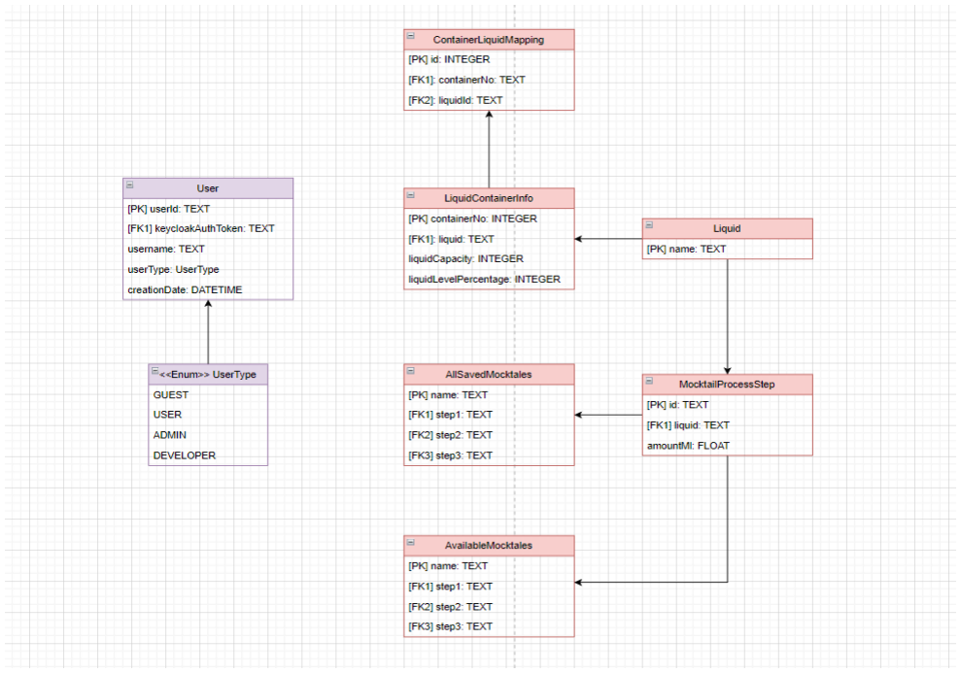
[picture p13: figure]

Figure 7. Machine-specific database schema.

In addition to the machine-specific database schema for each Mocktender, there will also be an internal management database schema to keep a record of machines, users, and the public Mocktail library, which will be a public collection of mocktails open for users to browse, make, and contribute to. Figure 8 below shows the structure for the management database schema.

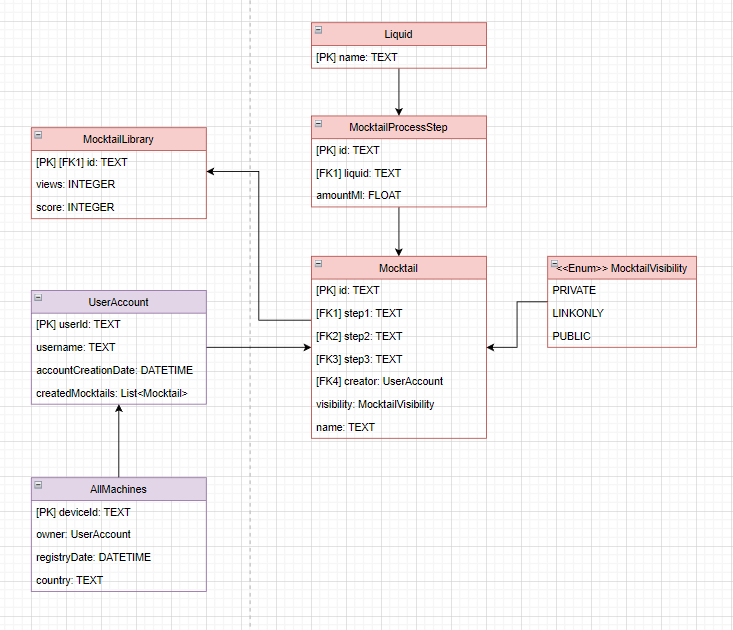
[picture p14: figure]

Figure 8. Cloud-Based Mocktail Management Schema.

## 3 Software Design

The Mocktender system will follow a Microservice architecture, with the core of the application being on the System Controller. The System Controller will make calls out to the microservices running beside it as needed. For the Mocktender, the system controllers are the 3 Raspberry Pi devices that control each node of the deployment diagram seen in Figure 2.

The implementation of the Mocktender will combine several languages and frameworks. The communication backbone of the system to send messages and commands between the nodes of the Mocktender will be implemented in JavaScript running in the NodeJS runtime environment. The Frontend Flask Webserver will be created using Python and rendered HTML templates.

The microservices will be developed using Python and will serve as the software interface for the Mocktender’s hardware devices. These microservices will be implemented using an object-oriented design pattern using GPIO Zero as the framework for the hardware interface.

### 3.1 Software Design for a UserInterface Node

The UserInterface node hosts a Flask web server as a frontend to the system, and an SQLite database (LocalDB) as a backend. It receives messages through connection to the Firebase Realtime Database (discussed in Section 3.4).

The frontend Flask webserver is hosted in the UserInterface node by the Raspberry Pi device. The Flask webserver will utilize the Flask library in Python to create and run the Flask web server, as well as HTML templates to render the desired web pages. The web interface flow chart showcasing the web pages rendered on the flask server is shows below in Section 5 (GUI Design).

The local backend consists of an SQLite database which will allow for storing local data received through the Firebase database about the liquid level, as well as recipes created through the user interface. The SQLite database is accessed by the Flask web server when user input is received. The sequences of data being received by the database are shown in the sequence diagrams in Section 2.3. The database schema is described above in Section 2.4. A flow chart showcasing the process of moving between the web pages on the Flask web server is shown in Figure 9 below.

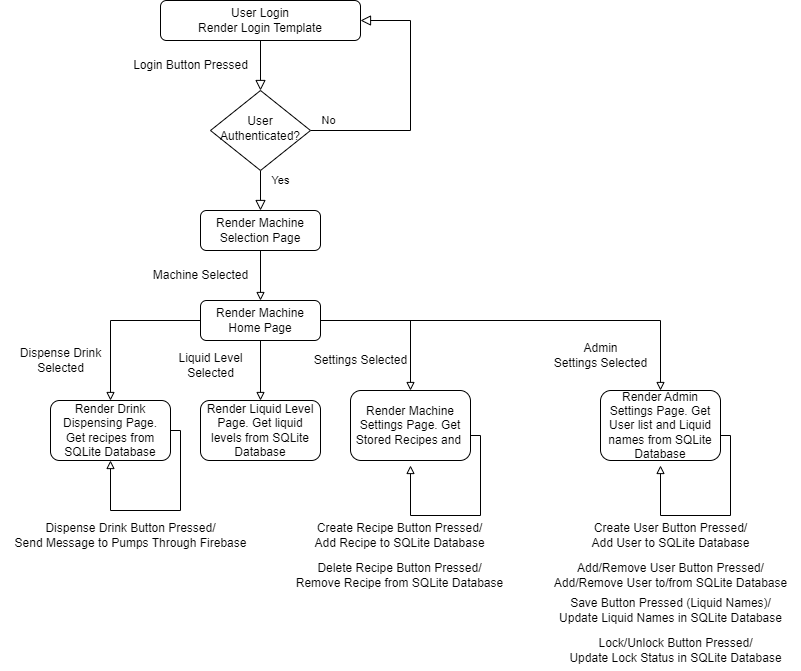
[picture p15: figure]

Figure 9. Flow Chart for Fronted Flask Web Server hosted by the UserInterface Node.

### 3.2 Software Design for Physical IOController Node

The IOController controls the hardware devices used for the Mocktender. Each IOController node has 3 liquid level sensors and 3 liquid pumps corresponding to the 3 liquids that can be mixed by the Mocktender. The IOController receives messages from the UserInterface which can either be a pump related command or a liquid level related command. The pumps that we are going to use for the Mocktender use DC Motors as the underlying actuator. This is modelled in the class diagram below (Figure
10) as the DCMotor class. UltrasonicSensor and DCMotor implement an interface of the same name which seems odd at first glance. It, however, allows for a more modular system if for example, it is decided to change out the DC Motors for stepper motors or, more relevantly, it is required to simulate hardware devices to prove a scalable system.

For the physical IOController node however, the UltrasonicSensor class will be composed of a DistanceSensor from the gpiozero library which provides an easy-to-use API for measuring distance. A LiquidLevelSensor will be composed of an UltrasonicSensor and the IOController will be composed of 3 LiquidLevelSensors stored in a list.

The DCMotor class will be composed of a Motor from the gpiozero library which will allow for the easy and precise control of a DC motor. A LiquidPump will be composed of a DCMotor and the IOController will be composed of 3 LiquidLevelSensors.

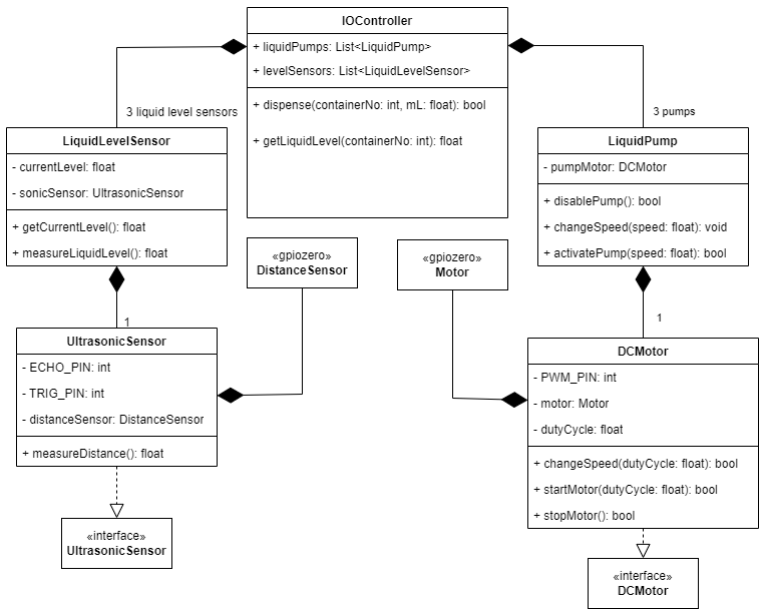
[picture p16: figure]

Figure 10. UML Class Diagram for the IOController Node.

### 3.3 Software Design for SystemSimulator Node

The SystemSimulator node acts as a proof-of-concept meant to demonstrate the scalability of the project. The SystemSimulator node is meant to be identical to the IOController node from the perspective of the UserInterface, except the input hardware in the IOController node will be simulated with software and the output hardware will be simulated with LEDs. In Figure 11 below, an UltrasonicSimulator notably has no association with a gpiozero DistanceSensor as the distance data will be generated randomly.

Additionally, the DCMotorSimulator implements a DCMotor and is composed of a PWMLED instead of a Motor. As an LED can be driven in the same manner as a DC motor, the implementation of the DCMotorSimulator would not need to be changed from the DCMotor class. The UltrasonicSimulator class implements a UltrasonicSensor but would need to be rewritten from the UltrasonicSensor class to generate random data representing distance. This can be seen in Figure 11 below in the UltrasonicSimulator block where a private method has been added to make random distances.

For the SystemSimulator node, a LiquidLevelSensor will be composed of an UltrasonicSimulator. A DCMotorSimulator will be composed of a PWMLED. A LiquidPump will be composed of a DCMotorSimulator. The SystemSimulator will be composed of 3 of each LiquidPumps and LiquidLevelSensors.


Figure 11. UML Class Diagram for the SystemSimulator Node.

### 3.4 Software Design for Backend Firebase Realtime Database

The cloud backend consists of a non-relational RESTful Firebase real-time database which will allow for internode communication. The database structure will resemble a tree, and each Raspberry Pi will be associated with a unique name. Messages intended for a given node will be sent under the node with the name associated with the desired destination Pi. Figure 12 below shows the bare-bones backend structure.

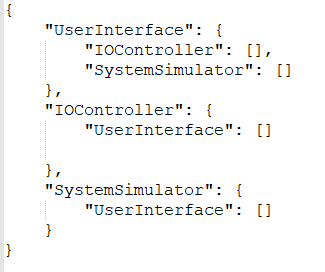
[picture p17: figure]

Figure 12. Backend Firebase Realtime Database Bare-bones Data Structure

## 4 Hardware Design

The hardware designs of the various components and subcomponents of the Mocktender system are discussed in the sections below.

### 4.1 Liquid Level Sensor

The liquid level sensors are part of the IOController subsystem and are responsible for measuring the volume of the liquids stored in the Mocktender. There will be three liquids that can be mixed at a time in the Mocktender. Each liquid will get its own liquid level sensor which is modelled below in Figure 13. The liquid level sensors will be implemented using 3 Ultrasonic Sensor (US) modules, specifically the HC-SR04 US. The HC-SR04 requires a 5V supply which can be provided using the Pi’s 5V pin. The US can communicate with the Raspberry Pi using a by sending a digital GPIO pulse to the TRIG pin (see Figure 13) and then interpreting the response on the ECHO pin as a digital data stream using GPIO.

The TRIG pin accepts voltages between 3-5V as a logical “1”. The GPIO pins on the Raspberry Pi can output 3.3V so the TRIG pin can connect directly to a GPIO pin. The ECHO pin however can output up to 5V. As this would damage the 3.3V GPIO pin on the Raspberry Pi, a voltage divider using 2 resistors in series will be used to drop the voltage at the GPIO pin down to 3V. The specific configuration can be seen below in Figure 13 The negative terminal of R1 and positive terminal of R2 will connect to the GPIO pin.

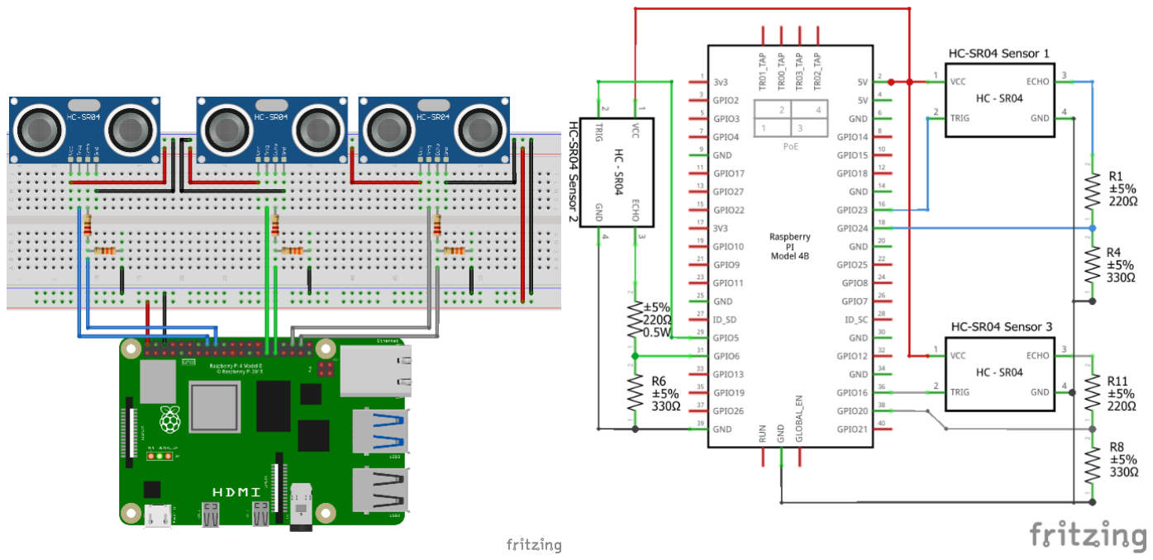
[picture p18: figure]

Figure 13. Breadboard and circuit schematic for Liquid Level Sensors

### 4.2 Drink Dispenser System

The Drink Dispenser System is a subcomponent of the IOController Subsystem. It is responsible for the controlled dispensing of the various liquids to be mixed. For the system, we will need 3 pumps which will each use a DC motor to actuate. The DC motors will use an H-Bridge module which will allow us to control the speed of the pumps using a PWM signal from the GPIO pins on the Raspberry Pi. The H-Bridge module we decided on uses the L298N Dual H-Bridge driver. The input pins on the H-Bridge driver accept voltages from 2.4-5V as logical “1” which means the 3.3V GPIO pins alone will be sufficient for controlling the motors. The H-Bridge driver can accept up to 12V to drive the motors. It also provides a stepped down 5V source which can be used to supply the Raspberry Pi with power. This can be seen below in Figure 14 as the orange wires. Since a single H-Bridge driver can only driver two motors at once, two drivers are required to meet our three liquid requirements.

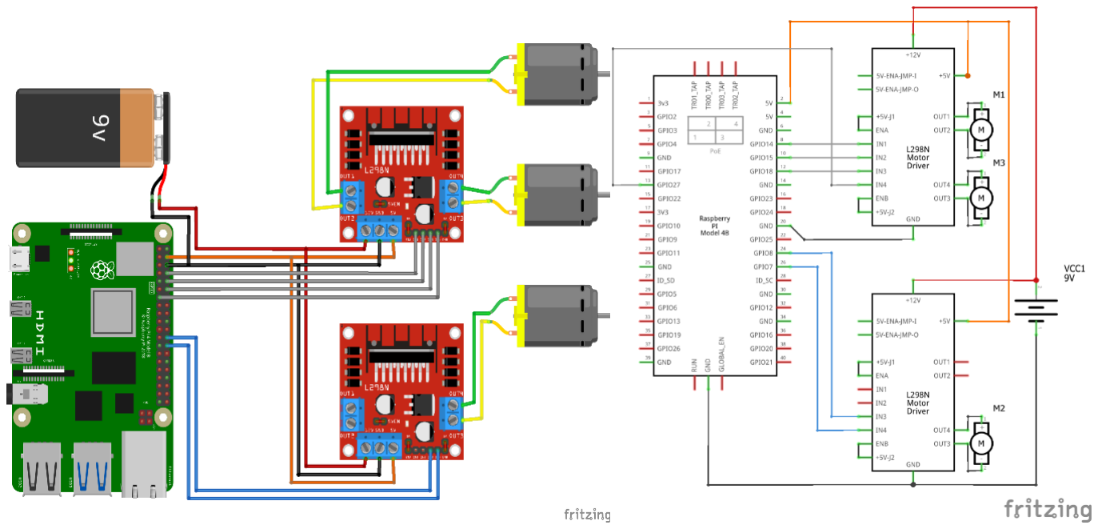
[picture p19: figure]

Figure 14. Drink Dispenser System component and circuit schematic

### 4.3 LCD Feedback System

The LCD (Liquid Crystal Display) Feedback system is a subcomponent of the IOController Subsystem. It is responsible for providing onboard visual confirmation for the active state of the system. The LCD used for the feedback system is a standard 1602 LCD, the numbers indicating that it is a 2 row LCD with each row containing 16 characters. The LCD can take 3.3V for power and for logical “1” meaning that it can be operated using the Raspberry Pi’s 3.3V power source and GPIO pins. A resistor must be placed between the VO pin on the LCD and ground to be able to read the text on screen which can be seen in the schematics in Figure 15 where a 2200Ω resistor has been placed between VO and the GND rail. The backlight of the LCD must also be powered to read the text on screen. This too can be seen below in Figure 15 where Pin 16 (LED-) is connected to GND and Pin 15 (LED+) is connected to the 3.3V power source through a 220Ω resistor.

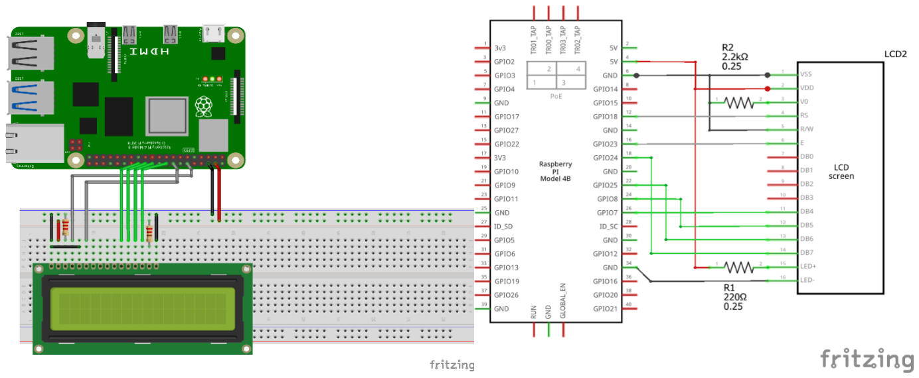
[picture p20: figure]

Figure 15. LCD Feedback System component and circuit schematic

### 4.4 IOController Simulator

To prove the scalability of the Mocktender, a Raspberry Pi device was reserved to be a shadow copy of the IOController Subsystem. It will simulate the function of the Sensor Subsystem, acting as a second machine. The Pump modules will be mimicked using LEDs, using the on state to pretend that the “pump” is dispensing the liquid and the off state to pretend that the “pump” is not dispensing anything. All LEDs have an associated “forward voltage” which is simply the voltage required to turn the LED on. This value is generally within 1.8-3.1V which is well within the 3.3V GPIO voltage. LEDs are unable to limit the current across them sufficiently while active, so series resistors (see Figure 16 below) are required to keep the current at or below 20mA to prevent damage to both the LED and GPIO pin.

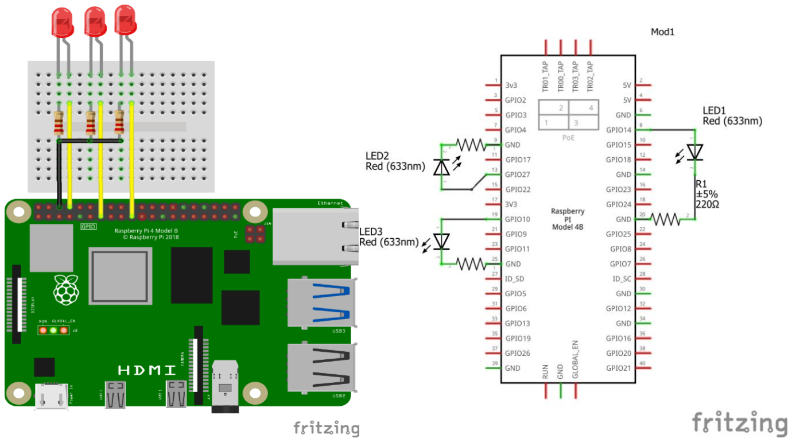
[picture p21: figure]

Figure 16. IOController Simulator Component and circuit schematic.

## 5 GUI Design

The graphical user interface of the Mocktender system serves as the user’s access to the system, providing liquid level information, dispensing, and recipe creation. The GUI will be hosted on a Flask webserver that uses HTML templates to graphically render web pages that a user can interact with (web interface). There are two types of users, an administrator, and a customer, whose roles are further outlined in Section 5.1 below. To provide an overview of the functionality of the web interface, a flowchart of the web pages can be seen below. A brief overview and wireframe showcasing each page of the web interface will follow in the Sections 5.1.1 – 5.1.7. A GUI Design flow chart is shown below in Figure 17. For information on the software design including a flow chart showcasing the rendering of pages and messages sent, refer to Section 3.1 above.

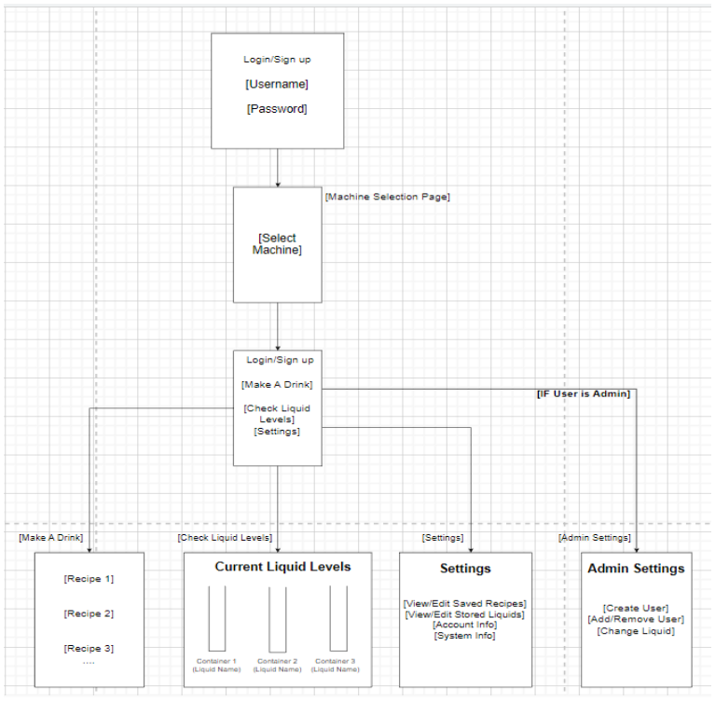
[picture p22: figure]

Figure 17. GUI design flow chart

5.1.1 User Login Page
When a Mocktender machine is received, an initial admin username and password will be provided. This will be used to login for the first time and access the Mocktender machine interface. The admin can then access the Admin Settings page and create new admin and customer accounts (discussed further in Section 5.2). The login page will take user input of a username and password, then send the data to the SQLite authentication database when the “login” button is pressed. If the login is accepted, the user will be redirected to the machine selection page discussed in Section 5.1.2, and if the login is denied, a message will inform the user that an incorrect username or password was entered. A wireframe showcasing the prototype design of the login page can be seen below in Figure 18.

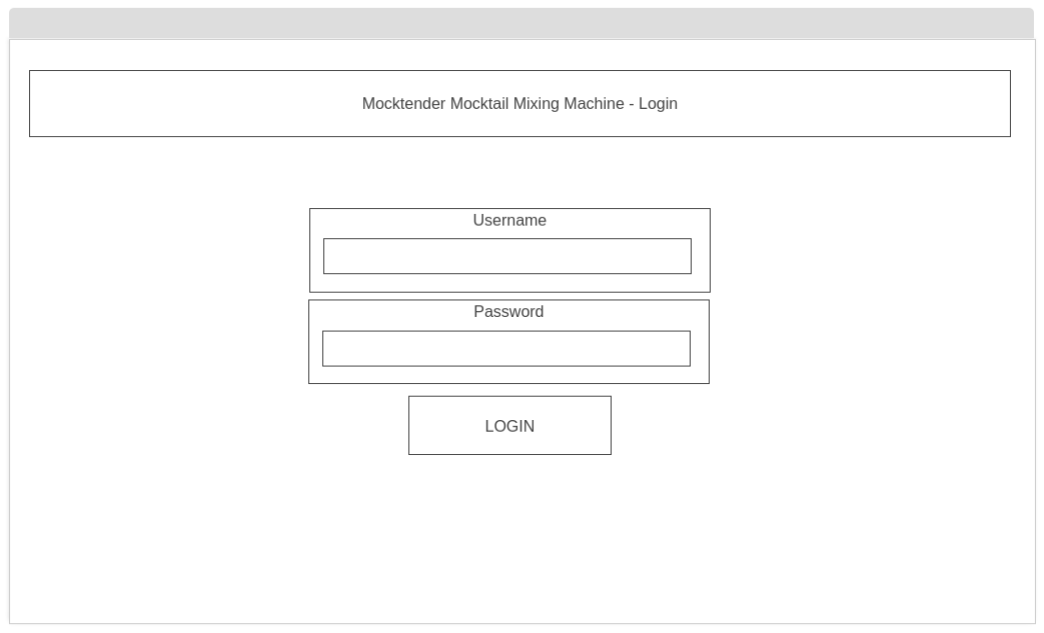
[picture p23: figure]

Figure 18. Wireframe of the Login page of the Web Interface.

5.1.2 Machine Selection Page
It is possible that a user is associated with multiple machines in the UserInterface system. The machine selection page will allow such a user to select which machine they would like to access. A list will be generated of the machines that the user has access to, and they will be able to select the machine to access and then press the “Select” button to access the home page of the machine (discussed in Section 5.1.3). A wireframe showcasing the prototype design of the machine selection page can be seen in Figure 19 below.

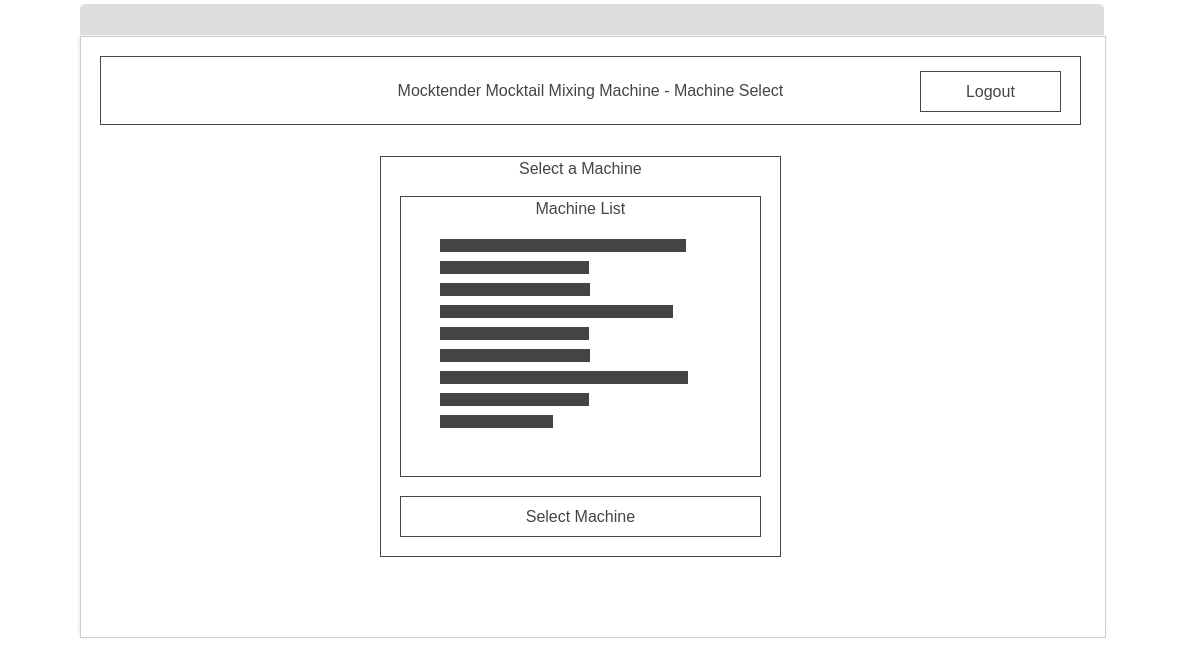
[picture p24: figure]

Figure 19. Wireframe of the Machine Selection Page of the Web Interface.

5.1.3 Machine Home Page
The machine home page allows for a user to select an action that they would like to complete. The action selections are, dispensing a drink, checking the liquid levels, accessing settings (recipe creation), and if they are an Admin user, accessing the admin settings. Each action option is associated with a button that will redirect the user to the page associated with that action. A wireframe showcasing the prototype design of the machine home page can be seen below in Figure 20.

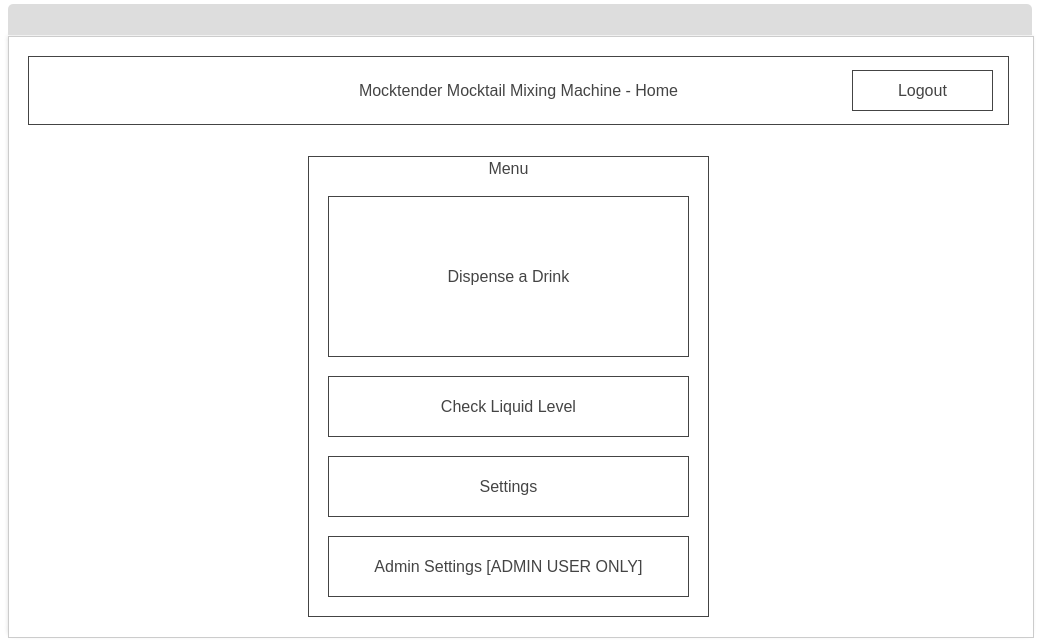
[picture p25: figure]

Figure 20. Wireframe of the Machine Home Page of the Web Interface.

5.1.4 Drink Dispensing Page
The drink dispensing page allows for the user to select a recipe from a list of recipes, and dispense the drink specified by that recipe. When a recipe is selected from the list, and the “Dispense Drink” button is pressed, the machine will dispense the drink. If the machine does not have the correct liquids, or not enough liquid, it will display an error message to the user and prompt them to select a different option. A wireframe showcasing the prototype design of the drink dispensing page can be seen in Figure 21 below.

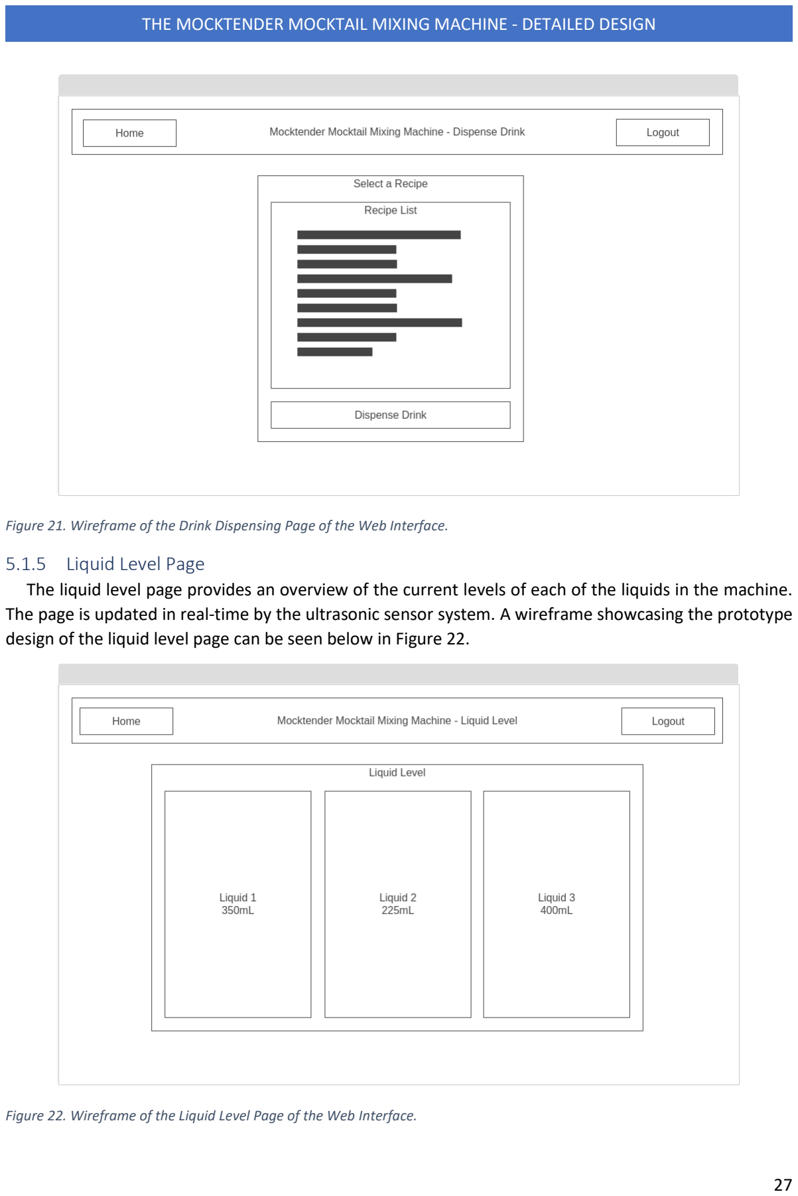
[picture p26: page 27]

Figure 21. Wireframe of the Drink Dispensing Page of the Web Interface.

5.1.5 Liquid Level Page
The liquid level page provides an overview of the current levels of each of the liquids in the machine. The page is updated in real-time by the ultrasonic sensor system. A wireframe showcasing the prototype design of the liquid level page can be seen below in Figure 22.

Figure 22. Wireframe of the Liquid Level Page of the Web Interface.

5.1.6 Settings Page (Recipe Creation)
The settings page allows for the user to create new recipes using the liquids currently in the machine and view the recipes currently stored in the machine. A recipe can be deleted by selecting it from the list and pressing the “Delete Recipe” button. The settings page also shows account and system information for the user. A wireframe showcasing the prototype design of the settings page can be seen below in Figure 23.

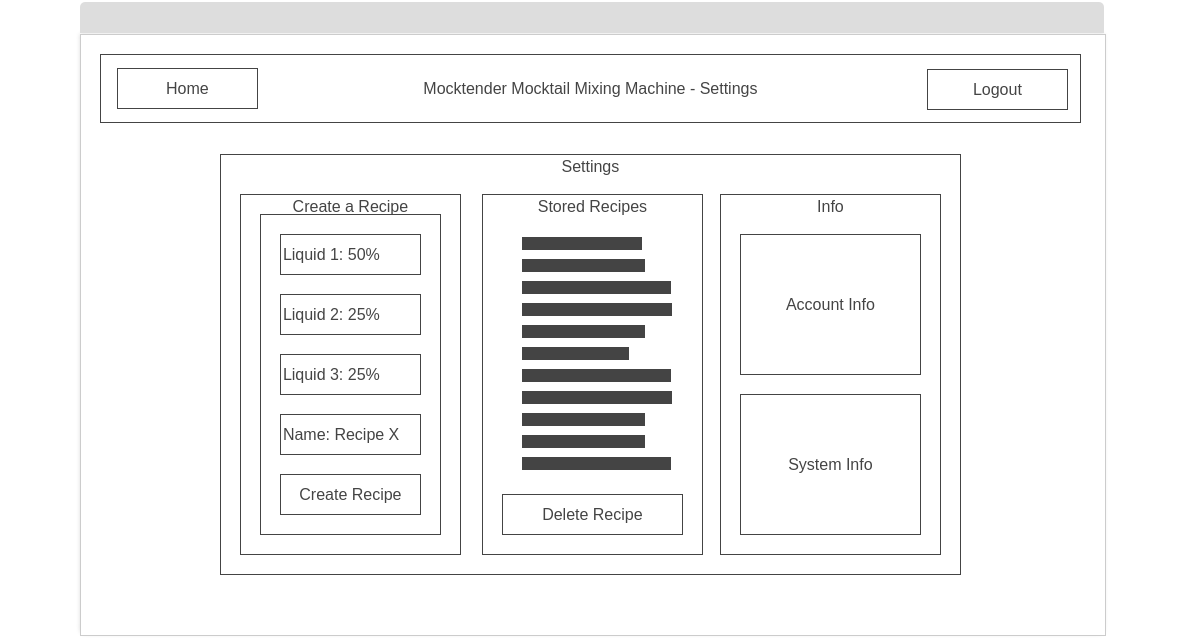
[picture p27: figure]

Figure 23. Wireframe of the Settings Page of the Web Interface.

5.1.7 Admin Settings Page
The admin settings page allows for an admin user (discussed in Section 5.2 below) to perform admin actions on the machine. These actions are, creating a new user, adding, or removing an existing user, changing the names of the liquids stored in the machine, and locking/unlocking the machine. To create a new user, under the Create a New User panel, the username and password of that user must be entered, and a selection of if the user is an admin or not must be made. The admin can then hit the “Create User” button to add the user to the system. The page will also display a list of all the currently registered users available in the system, and their status on the current machine under the User List panel. A user on another machine may be added, or a user currently on the machine can be removed using the “Add/Remove User” button. To liquid names can be modified in the text boxes under the Liquid Settings panel and will be saved when the user pressed the “Save” button. The “Lock/Unlock Machine” button in the Machine Admin panel allows for the admin to lock or unlock the machine. A wireframe showcasing the prototype design of the admin settings page can be seen in Figure 24 below.


Figure 24. Wireframe for the Admin Settings Page of the Web Interface.

### 5.2 Table of Users/Roles

The Mocktender system has two types of users that will interact with the machine. An administrator user who owns the machine, and a customer that has permission to use the machine. The descriptions are provided below in Table 5.1.

Table 5.2. Users and Roles in the Mocktender system.

User/Role | Description | Usage/Access
Administrator (Owner) | The owner of the Mocktender device. Can own 1 or more Mocktender devices that will be associated with their account in the database. For our project, one admin account will be associated with both the physical device and the simulation device. | The administrator has access to the admin settings page of the web interface in addition to all the other pages a user has access to. They can lock/unlock the machine, create or add/remove users, change liquids, as well as use the machine like a normal user.
Customer (Regular User) | A user of the Mocktender device that has an account authorized by the administrator to use the machine. An administrator can also be a consumer of the machine. | The user can access all pages of the web interface including, dispensing, liquid level, and the settings page of the user interface. If authorized on the device, a user can dispense the recipe of their choice, create a new recipe, or view the current liquids and their levels. If the machine is locked by the administrator, the user will be unable to use the remote dispensing functionality until it is reenabled.

## 6 Test Plans

The test plans for the Mocktender system for end-to-end communication, unit testing, and the final demo are outlined in the sections below.

### 6.1 End-to-end Communication Demo Test Plan

The Mocktender machine consists of multiple Raspberry Pi devices that need to communicate amongst each other to meet our project goals. The system is distributed between the Pi devices with one device hosting the front-end web interface for viewing the state of the machine and controlling the hardware devices. To facilitate node to node communication, a Firebase Realtime Database is used. The User Interface device is responsible for updating its local SQLite database with the liquid level sensor data received from the Firebase and sending instructions to the hardware devices. The IOController and SystemSimulator nodes receive and act on instructionsfrom the User Interface node, and send liquid level data to the UserInterface, both through the Firebase.

To test the end-to-end communication between the components, all the messages discussed in Section 2.1 will need to be created. The test scripts created will generate the messages, send them to the correct end destination, and the end destination will confirm that the message was received, and the contents are as expected. The test will pass if the message is the same as was expected, and will fail if either no message was received, or the contents are different than was expected. To provide test feedback, the messages will be printed to a console that will also be available on the Raspberry Pi devices whenever needed as a debugging option. The database contents on the Firebase real time database will also be tested after the messages are sent to ensure that the contents are as expected.

The following steps will be performed in our end-to-end testing demonstration:

1. First, the connections between the Raspberry Pi devices, and the Firebase real time database will be tested. A test script will verify that all the Pi devices are able to connect to the Firebase server.
2. Next, messages will be sent from the User Interface Pi device to the Sensor System and Simulation System to test that messages to control the motors can be received and acted on. These messages will go through the Firebase database.
3. The Sensor and Simulation Systems will then send messages to the User Interface Pi device through the Firebase to acknowledge that the message was successfully received, and the motors were run (drink was dispensed).
4. Next, sending the sensor data from the Sensor and Simulation Systems will be tested by using a test script to create mock sensor data to send to the User Interface System through the Firebase server.
5. The User Interface system will take the data from the Firebase cloud database and update its local SQLite database. The database contents will then be printed by the test script to showcase that they have been updated correctly.

6. Finally, the Flask web server sending messages will be tested by creating a demo Flask web page with a button that sends instructions to the IOController to pump a test recipe.

### 6.2 Unit Test Demo Test Plan

To test that each individual hardware and software component works as expected, the following hardware and software unit tests will be performed.

6.2.1 Hardware Testing
Table 6.2.1. Hardware device testing plan
Hardware Device Tester | Device Description | Test Description | Expected Test Results

Ultrasonic Sensor
(Liquid level
sensing)

Matt The ultrasonic sensor will be used to track the water level in the 3 liquid tanks in the Mocktender system. The distance from the sensor to the surface of the water is used to calculate the current volume of the liquid in the container.

To test the liquid
level system is
working correct,
measured amounts
of water will be
added and
removed from the
liquid containers.

The distance
from the sensor
to the surface of
the water should
match the
expected level
based on the
amount of water
added or
removed.

Peristaltic Pump
& DC Motor

Ethan The liquid pump will be used to dispense a drink. Based on the recipe provided by the user, each pump will be run for a specified amount of time so that the correct amount of each liquid is pumped (mixed) into the dispensed drink.

To test the
functionality of the
pump, the GPIO
pin connected to
the motor
controller will be
pulsed with PWM
signals. The PWM
duty cycle will
gradually increase
to 100% over 5
seconds, maintain
that 100% duty
cycle for another 2
seconds, and then
decrease to 0%
duty cycle over 5
seconds.

The user should
see the motor
gradually speed
up for 5 seconds
until it reaches its
max RPM,
maintain that
max RPM for 2
seconds, and
then see the
motor gradually
slow down for 5
seconds until it is
no longer active.
LCD Display | Duncan | The LCD display will display machine

To test the LCD
output, messages

The LCD display
should display

operation
information such as
what it is dispensing
and any errors.

will be displayed
on the LCD.

the correct
messages.
Simulation LEDs | Duncan | The simulation LEDs will light up when the motors on the simulation device are ON. Based on the recipe provided by the user, each LED will turn on for a specified amount of time so that it can be demonstrated that the simulation is working as expected.

To test that the
Simulation LEDs
accurately turn ON
when the motors
should be running,
the LEDs will be
pulsed with PWM
similarly to the
Peristaltic Pump &
DC Motor test. This
is since the
simulation LEDs are
simulating the
pump and motor
system

Similar to the
pump and motor
test, the user
should see the
LEDs gradually
get brighter as
the PWM is
increased until
they reach their
max brightness.
They will
maintain the
maximum
brightness for 2
seconds before
gradually slowing
down until they
are OFF.
6.2.2 Software testing
Table 6.2.2 Software testing plan
Software | Tester | Software Description | Test Description | Expected Test Results
Liquid Level Monitoring System | Matt | The liquid level monitoring system will take the sensor data and calculate the volume of liquid currently in the container in real time. It sends this information to the user interface to display to the user | To test the conversion from distance to liquid level, a simulated liquid level will be provided to the software and tested that the correct liquid level is output for sending to the user interface. | The calculated liquid level from the software should match the calculated liquid level when calculated by hand using the simulated data.
Motor Control System | Ethan | The motor control system takes the amount of liquid needed for the selected recipe and converts it into the | To test that the motor control system can convert the recipe into the correct PWM outputs for each of the motors, a sample | The time that the system “turns on the motor” should match the expected time

| | time that the motor needs to run based on the calculated flow rate. | recipe will be provided to the motor software, and it will be tested that it outputs the correct motor data. | based on the recipe and hand calculated flow rate.
Frontend Web Interface | Matt | The frontend web interface allows a user to view liquid levels, create recipes, and dispense a drink. It also allows an admin login to give administrative access to locking a machine and | The interface will be tested by rendering the components discussed in Section 5 and asserting that the outputs messages sent when buttons are pressed are as expected. A simulated liquid level will be sent to the interface and should display as corrected. | When a button is pressed, it should generate the correct message to send to the system. The liquid level should be received and displayed in the component correctly.
Backend Firebase Database | Duncan | The backend firebase database is used for internode communication in the Mocktender system. | The database will be tested using a script which generates messages to be sent over the database. | The database will be verified by pulling the stored information and testing that the information stored in the database is the same as the expected information to be stored in the database from the test script.
Local SQLite Database | Duncan | The local SQLite database is used to store machine specific data for display on the web interface. | The database will be tested using a test script which creates the expected tables outlined in Section 2.4. | The data stored in the SQLite database after the script is run will be pulled and compared with the expected contents of the database.

### 6.3 Final Demo Test Plan

To validate the finished Mocktender system, the following test plan will be used to show that the system functions as expected, and the requirements are met.

6.3.1 Automatic Liquid Mixing
The system must be able to automatically mix liquids as specified by the user. The correct amount of each liquid must be dispensed into the cup so that the drink is as expected. This will be tested by providing recipes with known liquid amounts and ensuring that the correct amount of each liquid was mixed and dispensed into the cup.

6.3.2 Administrative Access
The administrative access requirement of the system ensures ease of control of the system for use in a public place, and in a household. The administrator user can access the web interface and add new users, as well as lock the machine. To test this, an admin user will login, add a new user, that user will login and show that they can use the machine with the correct permissions. The admin user will also test the ability to lock the machine from non-admin users to be able to login.

6.3.3 Remote Dispensing Access
Remote dispensing access allows for a user to control the machine from the web interface to dispense their drink of choice. To test this, the web interface will be used to dispense a drink.

6.3.4 Recipe Creation and Storage
The recipe creation and storage requirement of the system allows for a user to create a new recipe and select a recipe from the database stored in the system. To test the recipe creation and storage, a recipe will be created by a user, and the database will be pulled to ensure that the recipe is present.

6.3.5 Remote Liquid Level Monitoring
The remote liquid level monitoring requirement of the system allows for a user to view the current liquid levels of the system in real time and for the machine to ensure that the selected recipe can be dispensed. To test this objective, a measured amount of liquid will be poured into an empty liquid container, and a liquid container with a known amount of liquid. The web interface should reflect that the measured amount was added, and if a recipe with too much of that liquid is selected, it should be denied.

## 7 Project Update

The Mocktender project has started slowly, however we have planned to mitigate the delays and get the project back on track for completion as scheduled. Our team had struggles completing the simulation system for the end-to-end demo, but we met as a group and discussed how to get back on track before the unit testing demo in two weeks.

Looking back at our proposal, most of our milestones still make sense and we are following them to continue work on our project. We are a bit behind schedule due to not receiving the hardware parts ordered from Digi-Key until March 10th, so the hardware components of milestones 3 and 4 had to be moved back. Work towards the software components of milestones 3 and 4 have gone well and are near completion. Once we receive the hardware devices, we will work to mitigate the delays to our schedule and keep the project on schedule.

The updated project milestones can be seen below in Section 7.1, and the updated Gantt chart showcasing our project timeline can be seen below in Section 7.2.

### 7.1 Project Milestones

The Mocktender system will continue to be developed following the milestones shown in the table below. Table 7.1 below was updated from the proposal to reflect updates discussed above in Section 7.

Table 7.1 Milestones for the Mocktender System

Milestone # | Name | Description | Date
1 Uploading and | Fetching Data | Computer devices can read from and write data to a real-time database independently of each other, which can then be accessed and displayed on an external device. | February 21st [Complete February 28th]
2 Communication | Between Nodes | Communication established between computer devices (HTTP etc.) to transfer data stored locally between nodes and issue commands. | February 28th [Complete March 10th]
3 Measurement | and Conditional Actuation | Liquid level of a fixed container can be measured accurately using sensors can uploaded to the database. Data can be used to turn on an LED when a threshold is reached. | March 3rd [All Hardware Moved to March 17 th]
4 Exposing Data | to the World | The liquid level of the fixed container will be displayed as text on a Flask web server, exposing the data to the world. The simulation system will display three liquid levels at once. | March 7th [All Hardware Moved to th] March 17
5 Hardware | Assembly | Assembled liquid dispensing system utilizing peristaltic pumps. Liquid level on webserver should be updated (as text) in real-time with data from the Ultrasonic sensor(s). | th March 14 [Moved to th] March 17
6 Graphical User | Interface | Webserver displays the volume of the liquid containers as an animation. Users can navigate between different webpages on the server. | March 21st
7 Controlling the | Hardware System with UI | Webserver component can control all 3 liquid pumps implementing the drink mixing. Users can login and save customs mixtures locally and in the real-time database. | March 28th

### 7.2 Schedule of Activities

Our updated Project Gantt Chart can be seen below in Figure 25. Green indicates completed items, yellow indicates items in progress, and red indicates items not yet started.

Feb 1; Feb; Feb 1 Mar 1; Mar 1; Mar

Figure 25. Updated Gantt Chart for the Mocktender project

Ma | Feb 1 Feb | Feb Mar 1 | Mar | Mar 1 Mar 1 | Mar
Ethan | Feb 1 Feb | Feb Mar 1 | Mar | Mar 1 Mar 1 | Mar
Duncan | Feb 1 Feb | Feb Mar 1 | Mar | Mar 1 Mar 1 | Mar

Feb 1 Feb 1

Mar Apr

Mar 1

Mar

Apr

## References

[1] Colourful drinks, abstract, new, HD wallpaper. Peakpx. (n.d.). Retrieved February 2023, from https://www.peakpx.com/en/hd-wallpaper-desktop-gfuhh.
[2] Cox, K. (2021, October 12). NielsenIQ: Newly Released Low & Non-alcoholic beverage trends. Wine Industry Advisor. Retrieved February 2023, from https://wineindustryadvisor.com/2021/10/12/nielseniq-newly-released-beverage-trends.
[3] Mocktails are gaining popularity. will meetings and events catch the trend? Meetings Today. (n.d.). Retrieved February 2023, from https://www.meetingstoday.com/articles/143402/mocktails-gaining-popularity-will-meetings-events-catch-trend. (https://www.meetingstoday.com/articles/143402/mocktails-gaining-popularity-will-meetings-events-catch-trend)
[4] Turcotte, S. (2023, January 12). Here's why alcohol-free drinks are gaining in popularity. CTV Kitchener. Retrieved February 2023, from https://kitchener.ctvnews.ca/here-s-why-alcohol-free-drinks-are-gaining-in-popularity-1.6227268. (https://kitchener.ctvnews.ca/here-s-why-alcohol-free-drinks-are-gaining-in-popularity-1.6227268)

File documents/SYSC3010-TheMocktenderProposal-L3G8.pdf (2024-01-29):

# SYSC3010 | Computer Systems Development Project

# Project Proposal

Group L3-G8; February 8th, 2023

Figure 1. Example of mocktail drinks to be made by the Mocktender machine [1].

Matt Reid, 101140593
Ethan Bradley, 101158848
Duncan MacLeod, 101160585
TA: Roger Selzler

THE MOCKTENDER MOCKTAIL MIXING MACHINE - PROJECT PROPOSAL

## Table of Contents

## 1 Introduction

The purpose of this document is to respond to the SYSC 3010 course requirement to produce a project proposal for our group, L3-G8’s project, The Mocktender Mocktail Mixing Machine. It is an IoT (Internet of Things) automated mocktail mixing machine. This document outlines the motivation, objectives, and goals behind the system as well as the project flow including use cases, a deployment diagram, and a flow chart.

### 1.1 Background

A mocktail is a non-alcoholic drink that captures the essence of a cocktail without the downsides of alcohol consumption. From work offices where you want to stay sharp while having fun drinks for lunch to wanting a healthier alternative to drinking cocktails at home, there are lots of reasons to enjoy a mocktail. As more people look towards health and wellness trends, the number of people drinking non-alcoholic beverages is rapidly increasing. A NielsenIQ study in October 2021 found that non-alcoholic beverage sales had gone up 33.2% in 12 months to a total market of $331 million [2]. In the United States, 30% of people who are of drinking age do not drink alcohol [3], and according to a 2021 survey by Statistics Canada, 1 in 5 Canadians said they have been drinking less than before the COVID-19 pandemic [4].

The at home cocktail drinking market has also grown significantly during the COVID-19 pandemic, with one in four people now spending more on home drinking than they did before [5]. The cost of a bartender for a private even can cost upwards of $50 per hour [6]. To provide the ease of having drinks at home or private events without needing to buy equipment and learn how to mix them yourself or paying a bartender, machines such as The Bartesian allow the creation of at home cocktails, mocktails, and margaritas using fillable drink containers and pods [7]. This device allows you to fill containers, set strengths, and creates a wide array of drinks, however it is restricted to drinks that are set by the pods and does not allow recipe creation or remote container liquid level tracking. Our solution will provide the ability to use a remote web interface to create new recipes, view real-time liquid levels, and admin access for usage at events.

### 1.2 Motivation

For mocktail drinkers that want to enjoy a drink at home, the time spent measuring and mixing the drinks can be prohibitive. For private event managers, the cost of hiring a bartender to make drinks to impress their client can be enormous. To help reduce the time strain of making mocktails, and remove the need to hire a bartender, The Mocktender Mocktail Mixing Machine is an IoT machine perfect for the at home mocktail consumer, and an event manager looking to impress their guests. For at home users, the recipe creation system allows users to specify their own recipe and measurements to make them the perfect mocktail in seconds with minimal mess. For event managers, the web interface allows remote tracking of liquid amounts to know when it needs filling, and it removes the cost of hiring a bartender to create mocktails.

### 1.3 Project Objective

The objective of the project is to create an automated mocktail mixing machine that provides a web interface to allow real-time liquid level monitoring, and recipe creation. It replaces the need for at home mixing equipment, and bartenders at events to eliminate the inflated cost of making mixed drinks. It will provide timely mocktails from specified recipes, allowing for easy access to healthier drinks and less time spent mixing with more time spent drinking.

### 1.4 Specific Goals

To create an easy to use and fully functional mocktail mixing machine, The Mocktender has the following goals in order of descending priority:

Automatic Liquid Mixing: The machine will automatically mix liquids together based on defined recipes in a database. The database will contain recipes that specify liquid percentages, and the Raspberry pi will use a pump to dispense the correct amount of each liquid into a cup.

Remote Liquid Level Monitoring: The machine will allow users to view the current liquid levels through an online web interface. An ultrasonic sensor will be used to provide real-time updates of the liquid levels. Notifications will be sent to registered users that liquid levels are low.

Recipe Creation and Storage: The machine will allow users to create new recipes in the web interface and store them in the database. Recipes consist of liquid names and the percentage that should be put in the cup.

Remote Dispensing Access: The machine will allow users to access the drink pouring menu remotely on the web interface. GUI (Graphical User Interface) buttons will be available to dispense selected drink recipes.

Administrative Access: The machine will allow an admin user to login to the web interface and lock the machine from use or modify the liquid types that are available in the machine. There will also be a clean function allowing for a liquid to be emptied from the machine and water to be used to flush out the pipes.

## 2 System Design

### 2.1 System Overview Diagram

The Mocktender consists of three main subsystems with an additional cloud infrastructure, which is illustrated by Figure 2 below. It may appear confusing at first that Figure 2 includes two instances of a UI and a database. The local services function as an endpoint for the user to interact with directly. Through the local UI, an owner can configure Keycloak authentication to allow access to the cloud infrastructure. The purpose of the cloud UI and database is for security and reliability purposes. For example, the cloud infrastructure would allow the user to use the web interface even when the Mocktender is not active and not running anything locally. One function of the cloud UI is the ability to activate the Mocktender and interact with it remotely.

The three subsystems not on the cloud are each managed by a different Raspberry Pi. The first Raspberry Pi is the “System Controller,” which is responsible for hosting the local infrastructure and facilitating communication between subsystems. Since the System Controller hosts the user endpoints, it effectively acts as an adapter proxy between the other entities which include the user, the local UI and database, the cloud, and the other subsystems. Aside from the web infrastructure, the Mocktender will also be physically equipped with an LCD display and a joystick for the user to operate the machine directly instead of through a web UI. The LCD display will be controlled by a different Raspberry Pi called the “Output Controller.” The Output Controller is responsible for controlling/managing every output peripheral in the system, which comes down to the LCD display and the pumps for pouring the liquid. The last subsystem is called the “Input Controller” which manages the inputs to the system and feeds any significant events to the System Controller.


Figure 2. Deployment diagram of The Mocktender Mocktail Mixing Machine

Figure 3. Rough Sketch of Internal Systems

2.1.1 Communication Protocols
The liquid level sensors and the pump controllers can be communicated with using GPIO as they operate on digital signals. Similarly, the LCD display can also be controlled using GPIO. The pump controllers will use stepper motors, and as such require a stepper motor driver to operate properly. The temperature sensor on the SenseHat can be read from using the I2C bus on the Raspberry Pi. Manual controls on the frame of the machine also produce digital signals, such as button presses. The Joystick produces analog signals, so it will be connected to the computer device using an Analog to Digital converter.

A Raspberry Pi node will upload to and read data from the real-time database. This node will communicate this data between nodes using an SPI connection, allowing for a concurrent 2-way communication stream. The Raspberry Pi will issue and receive commands from the other devices on the SPI bus, allowing the system to react quickly in real-time in response to unforeseen stimuli.

### 2.2 Component Details

The Mocktender will by comprised of 5 main systems. A local and cloud-based database will be used to store recipes that users create on the front-end User Interface. The front-end will also allow them to login and monitor the liquid levels in the systems and will allow them to be notified when the Liquid Level sensor system detects that the amount of fluid remaining in a container is running low. The user can use the Manual user input system or the Front-end User Interface to activate the Drink Pump system to dispense their drink.

2.2.1 Real-time and Local Databases
The first component proposed is the database model. As seen in Figure 2, the Mocktender will have both a local instance and a cloud instance, which will be synchronized. In the case that changes are made to the cloud database when the local database is offline, a change log file is generated and stored in a cloud VM, and the location of the log file is recorded in the database table “DatabaseChangeLogRef.” Permission to view/edit certain tables will be managed via Keycloak. The database schema can be split into a few categories, which are colour coded as shown in Figure 4. Database tables in red store data that is primarily used for the Mocktender’s main function, creating mixed drinks. Database tables in purple and the Keycloak table are related to user information and authentication. Tables in green are used for synchronizing the local and cloud instances.


Figure 4. Database Schematic of The Mocktender

2.2.2 Drink Pump System
The second component proposed for the Mocktender is the Drink Pump System. To have precise control over how well a drink is mixed, each of the 3 liquids added to the drink needs to have its own liquid pump module. A liquid will be stored in a container until GPIO signals are sent to a stepper motor, which will be used to implement a liquid pump and can be see below in Figure 5. As even small motors are capable of drawing hundreds of milliamps [8], it is essential that there is sufficient power distribution to ensure that the pumps do not become unresponsive. This is modelled in Figure 5 as an additional power bank connected only to the stepper motors.


Figure 5. Drink Pump schematic view of the OutputController subsystem

2.2.3 Manual User Input System
The third proposed system is the Manual User Input system. As the Mocktender is a drink mixing machine, it should not require an internet connection to be used. As such, a physical input system will be included in the system. Figure 6 below shows a computer device interfacing with an LCD screen as well as a rotary encoder with an internal button. Options will be shown on the LCD for a user to select their drink preferences, and the encoder can be used to confirm their selection. If the user has credentials to input, their recipes will be saved to a local database in the system which will be uploaded to the cloud database when a connection becomes available. The LCD module can be controlled using GPIO or I2C depending on the hardware available. The rotary encoder does not require analog-to-digital conversion which makes it the ideal choice for hardware input with a Raspberry Pi.


Figure 6. Schematic view for the manual user input system

2.2.4 Liquid Level Sensor System
The fourth proposed system for the Mocktender is the Liquid Level Sensor. The system will use ultrasonic sensors to detect the how far away the level of a liquid is from the lid of a container. The ultrasonic sensors can be controlled using GPIO and the data measured from the sensors will be used to graphically display the liquid level on the front-end graphical user interface. The computer reading the sensor data will communicate with the computer interfacing with the real-time database to ensure that there is always updated liquid level data on the front-end. Figure 7 below shows how the ultrasonic sensors will connect to a computer device. Each Ultrasonic sensor requires 2 pins, 1 for triggering the sensor and 1 for reading the data as a digital data stream.


Figure 7. Schematic view for the liquid level system, managed by the Input Subsystem

2.2.5 Front-end User Interface
The fifth component being proposed for the Mocktender is the Front-end user interface. The Front-end will be hosted on a webserver on one of the Raspberry Pi’s in the system and will be the main source of interaction between the system and the end-user. It will be built using React web design principles to provide an easy-to-use interface to the user. Figure 8 below shows a model of a potential use-flow of the front-end, using links to navigate to different webpages that organize related tasks into one spot. The user will be able to view their Mocktender’s current liquid levels in real-time and create Recipes based on the current combination of liquids in the system. The user will also be able to subscribe to notifications using their preferred method (e.g., Email, SMS, Push notifications). One user’s information will be hidden from another user by requiring them to login with a password.


Figure 8. Preliminary core page layout for the user interface

### 2.3 Use Cases

2.3.1 Use Case 1: MakeDrink
The most basic use case demonstrating the process to make a drink is the MakeDrink use case. This can be done through the web interface and manually through the machine itself. Figure 9 demonstrates the use case of making a drink via interacting with the machine directly. The Mocktender will be equipped with a simple interface consisting of an LCD display and a joystick. The LCD display will show all the saved Mocktails that are currently available for pouring. The user will be able to use the joystick to select the drink they want to make. When the user confirms their choice, the SystemInterface will pour the drink by communicating with OutputController by signalling which pumps to stop and start. When the drink is done, the LCD display will say “Enjoy.”


Figure 9. Sequence diagram for MakeDrink use case

2.3.2 Use Case 2: MakeRecipe
The MakeRecipe use case outlines the basic flow of the process to create a new mocktail recipe, which is done through the web interface. Figure 10 shows the process of interacting through the web interface to create a recipe. The user navigates through the web interface by going to “Settings” ->” Update UI” ->” View/Edit Saved Recipes.” From there, the user will be able to specify a sequence of drinks to pour to create their new mocktail. Once saved, the new mocktail is now available to make.


Figure 10. Sequence Diagram for MakeRecipe use case

2.3.3 Use Case 3: CheckLiquidLevel
The Mocktender is equipped with sensors to track how much liquid is left in each container, which the user can view through both the physical display and the web interface. The web interface is more comprehensive and easier to use, so Figure 11 demonstratesthe use case for checking liquid levels via the web interface. The user must be an admin to view the liquid levels. In practice, an “admin” account would correspond to someone or a group of people who own the machine.


Figure 10. Sequence diagram for CheckLiquidLevel use case

## 3 Work Plan

### 3.1 The Project Team

The Mocktender Project team, L3-G8, is composed of Matt Reid, Ethan Bradley, and Duncan MacLeod. Matt is interested in communications between devices and has strengths in documentation and backend database development. Ethan likes to design and build circuits and has strengths in creating schematics and implementing hardware designs. Duncan enjoys Android app development and has strengths in frontend development and user interfaces.

3.1.1 Roles and Tasks
Table 1. Assignment of major tasks to team members
Major Task | Primary | Secondary
Ultrasonic sensor water level data collection | Ethan & Matt | Duncan
Achieve communication between the three Raspberry Pi devices | Matt | Ethan
Create frontend user interface with admin login | Duncan | Matt
Construct machine frame and component housing | Ethan & Matt | Duncan
Create backend Firebase real-time database | Matt & Duncan | Ethan
Design circuit for electronic devices | Duncan & Ethan | Matt
Create pump mechanism for mixing drinks | Ethan | Matt
Integrate sensor data and pump mechanism with database | All Members | N/A
Connect all systems together | All Members | N/A
Perform full testing on all systems | All Members | N/A

Table 1 outlines the assignment of major tasks of building The Mocktender machine to members of the team. The primary assignments were selected based on the strengths of team members and what they are interested in learning during the SYSC 3010 course.

For the sensor data collection, Ethan is experienced with connecting sensors, and Matt wanted to learn more about sensor connections. Matt will work on communication between devices and Duncan will work on the frontend as they play into their strengths. For building the machine frame and component housing, Ethan and Matt were selected as they both has experience with building frames for projects.

The database will be worked on by Duncan as he has previous work experience and Matt as he has not worked with databases previously and is interested in learning. For the pump mechanism, Ethan was chosen as he is strong with creating circuits and mechanisms so is a perfect fit for making pump mechanisms with stepper motors. Ethan is working on circuit design as it is his strength and Duncan is joining as it is a major learning interest.

The rest of the tasks including integration with the database, system connection, and testing are all being worked on by all team members due to the tasks being centered on the entire system at once and is beneficial for all team members to understand.

3.1.2 Teamwork Strategy
As a team we will work together in an Agile sprint-based workflow to ensure that deadlines are followed, and tasks are organized. We will have a meeting every week to discuss the last weeks tasks and completions and identify the new sprint items for the upcoming week. If there are any items not completed from the week before, the reasons why will be discussed, and it will be completed as soon as possible. Our group will communicate both in person for sprint meetings and throughout the week on Microsoft Teams.

When code is completed, it will be reviewed by the secondary team member assigned to each task in Table 1 using GitHub pull requests. GitHub will be used for all the code for our project as it allows for continuous sharing source code between members and organization of changes and issues that were made/solved. Throughout the development process, any issues identified will be added to GitHub’s issue tracking system so that they are organized and can be referenced during the weekly sprint meetings.

3.1.3 What we will need to learn
The Mocktender implements technologies with various levels of understanding by our group members. During the project timeframe, we will need to learn front-end development and design, serial communications between devices, designing circuits with sensors/actuators, and integrating mechanical systems with electrical components.

Front-end development and design will be used to create the web interface. It will require learning JavaScript and React web design principles to create a functional and easy to use GUI.

Implementing a cloud-based infrastructure will require familiarization with the Google Cloud Platform and its functionalities, as well as the third-party services that typically accompany it, such as Keycloak and Ngrok.

Serial communications between devices will be used to send sensor data to the user interface subsystem and send recipe data to the pump control subsystem. It will require building on skills in using SPI communications between devices.

Learning to design circuits with sensors/actuators will be needed for building the ultrasonic water level sensor and transferring liquids using pumps. This will require learning soldering and integrating ports required by the ultrasonic sensor and pump motors.

For integrating mechanical systems and electrical components, we will need to learn protocols for sending electrical data to the mechanical systems.

### 3.2 Project Milestones

To structure the implementation and design of the Mocktail Machine, we have broken up our timeline into 7 milestones which can be seen in the table below.

Table 2. Project milestones with deadlines.

Milestone # | Name | Description | Date
1 | Uploading and Fetching Data | Computer devices can read from and write data to a real-time database independently of each other, which can then be accessed and displayed on an external device. | February 21st
2 | Communication Between Nodes | Serial communication established between computer devices (I2C, SPI, etc.) to transfer data stored locally between nodes and issue commands. | February 28th
3 | Measurement and Conditional Actuation | Liquid level of a fixed container can be measured accurately using sensors can uploaded to the database. Data can be used to turn on an LED when a threshold is reached. | March 3rd
4 | Exposing Data to the World | Two additional containers with liquid level measuring will also have their data uploaded to the database. The liquid level will be displayed as text on a webserver | March 7th
5 | Hardware Assembly | Assembled liquid dispensing system utilizing peristaltic pumps. Liquid level on webserver should be updated (as text) in real-time. | March 14th
6 | Graphical User Interface | Webserver displays the volume of the liquid containers as an animation. Users can navigate between different webpages on the server. | March 21st
7 | Controlling the Hardware System with UI | Webserver component can control all 3 liquid pumps implementing the drink mixing. Users can login and save customs mixtures locally and in the real-time database. | March 28th

### 3.3 Schedule of Activities

Figure 12 below outlines the timeline of milestone activity completion as a Gantt chart over the 2 months working on our project. The milestones are outlined on the right, and the black lines represent when the activities will be worked on.


Figure 11. Project Gantt Chart
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

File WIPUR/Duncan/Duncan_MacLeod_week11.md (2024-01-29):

## Weekly Individual Project Update Report
### Group number: L3-G8
### Student name: Duncan MacLeod (101160585)

### Week 11 (March 29th - April 4th)
___
1. **How many hours did you spend on the project this week?** 25 hours

2. **Give rough breakdown of hours:**
	1. Re-worked web interface layout
	2. Implemented proper API functionality for Firebase end to end communication
	3. Met with team to integrate the entire system into the frame and plan last steps: meeting/construction 6 hours

3. ***What did you accomplish this week?***
	1. The last major API functionality was implemented
	2. Performed integration testing with rest of group
	3. Recorded the final video for our project
  
4. ***How do you feel about your progress?***
	We made a lot of progress this week. The last couple weeks have been extremely pivotal and this past week was
	another good follow-up. I think we can hit all the major parts of our original scope.

5. ***What are you planning to do next week***? 
	1. Implement the functionality to add users and send notifications
	2. Make the web interface appear more aesthetic, as it is currently very grey-ish and blank.
	3. One the additional functionality is implemented, perform unit testing on the new functions and then re-perform
	integration testing on our project as a whole.
	4. Work on the final report for our project.

6. ***Is anything blocking you that you need from others?*** 
	- Nothing is blocking me.

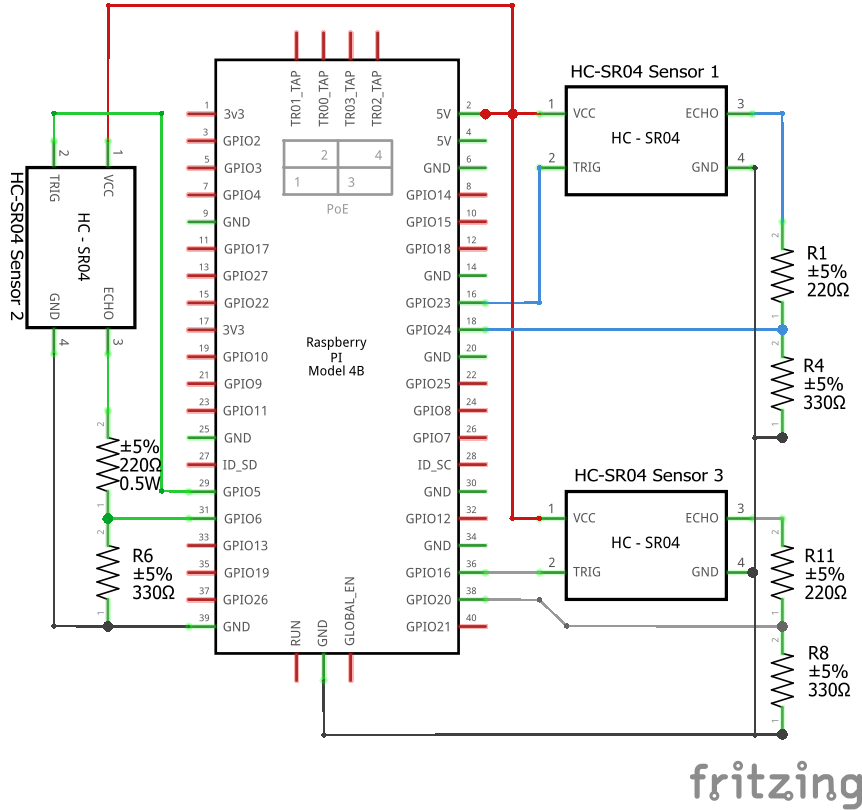
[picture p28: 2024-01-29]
schematics/liquid_level_system/liquid_level_schem.png

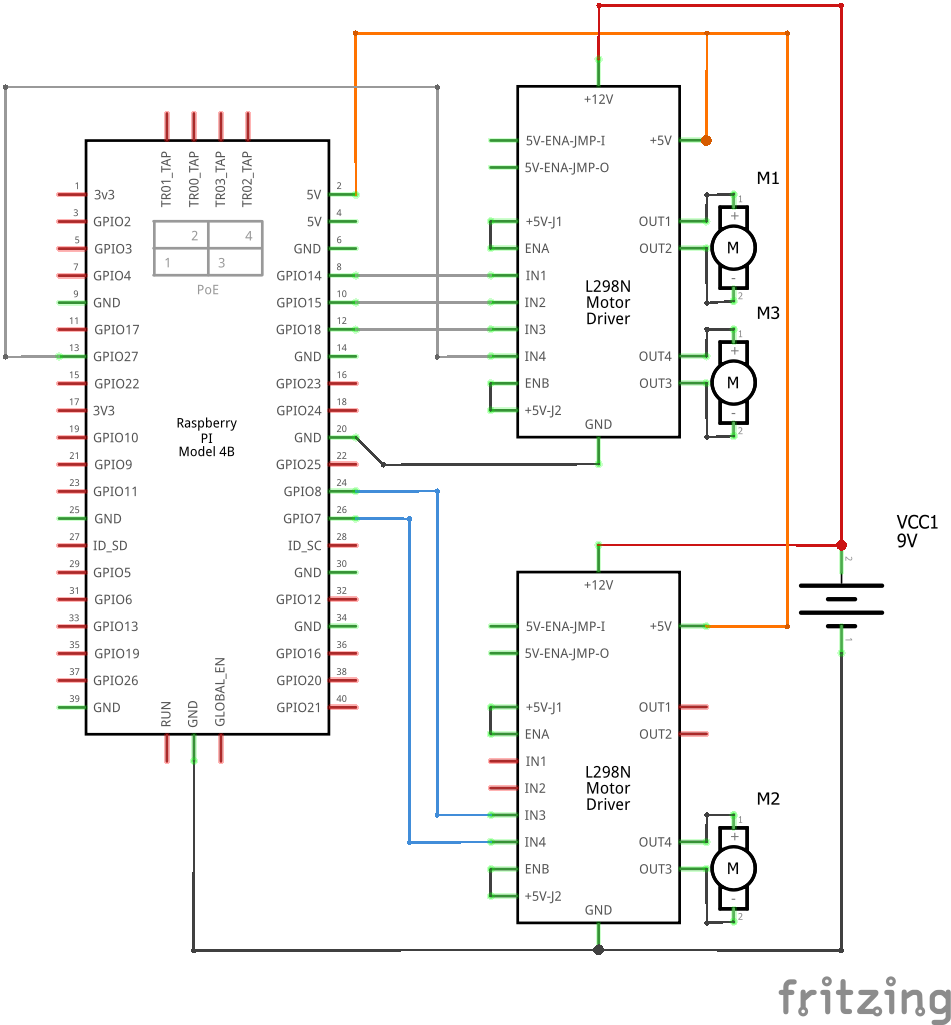
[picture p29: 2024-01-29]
schematics/pump_control_system/pump_controller_schem.png

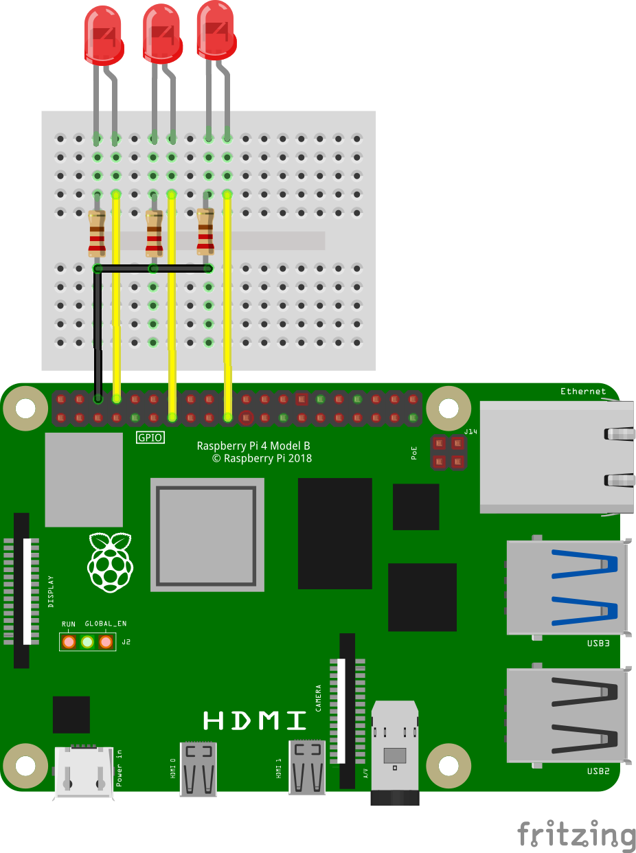
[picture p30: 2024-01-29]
schematics/simulation_system/simulation_bb.png

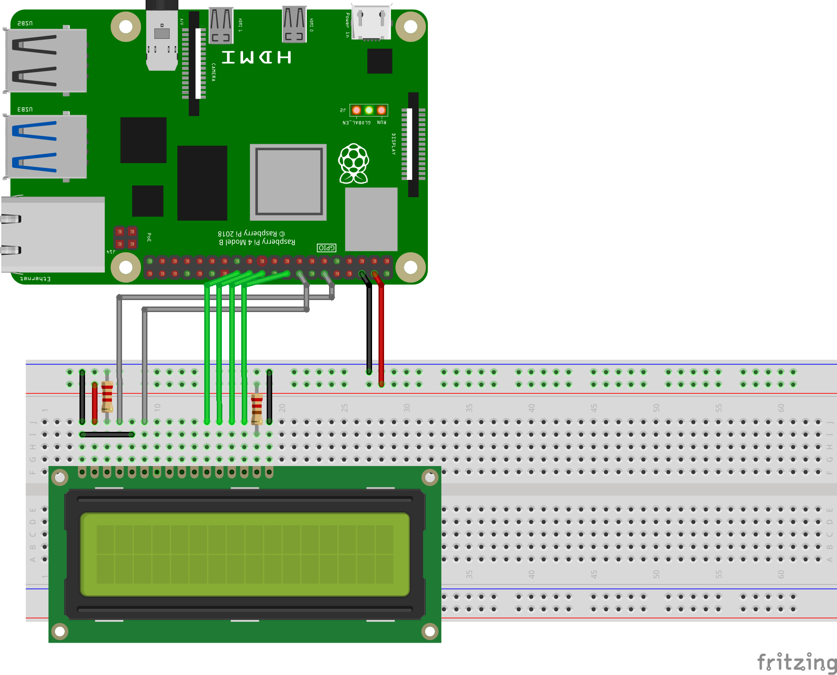
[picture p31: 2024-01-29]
schematics/temp_output_system/temperature_sense_hat_bb.png

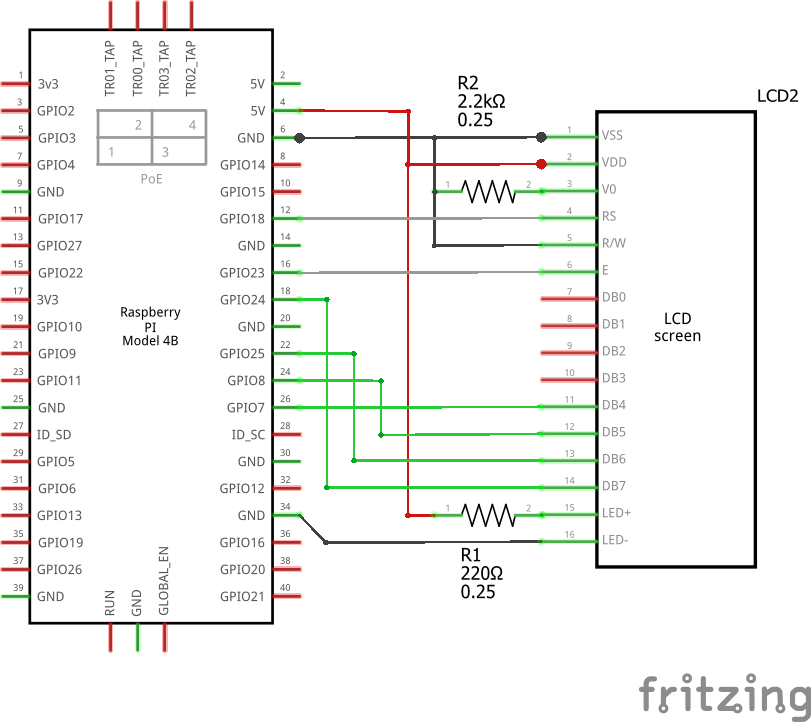
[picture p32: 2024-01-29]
schematics/temp_output_system/temperature_sense_hat_schem.png

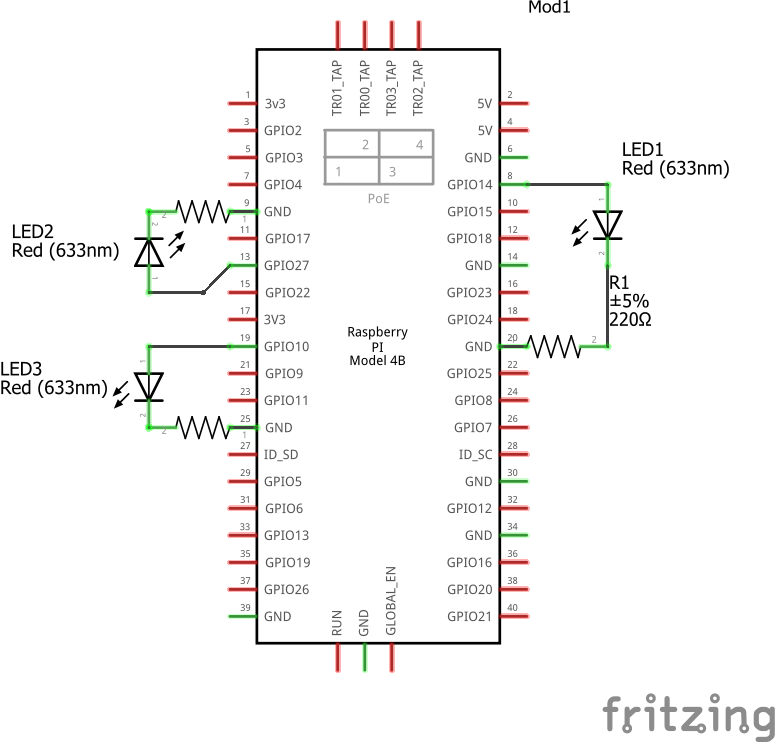
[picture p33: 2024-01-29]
schematics/simulation_system/simulation_schem.png

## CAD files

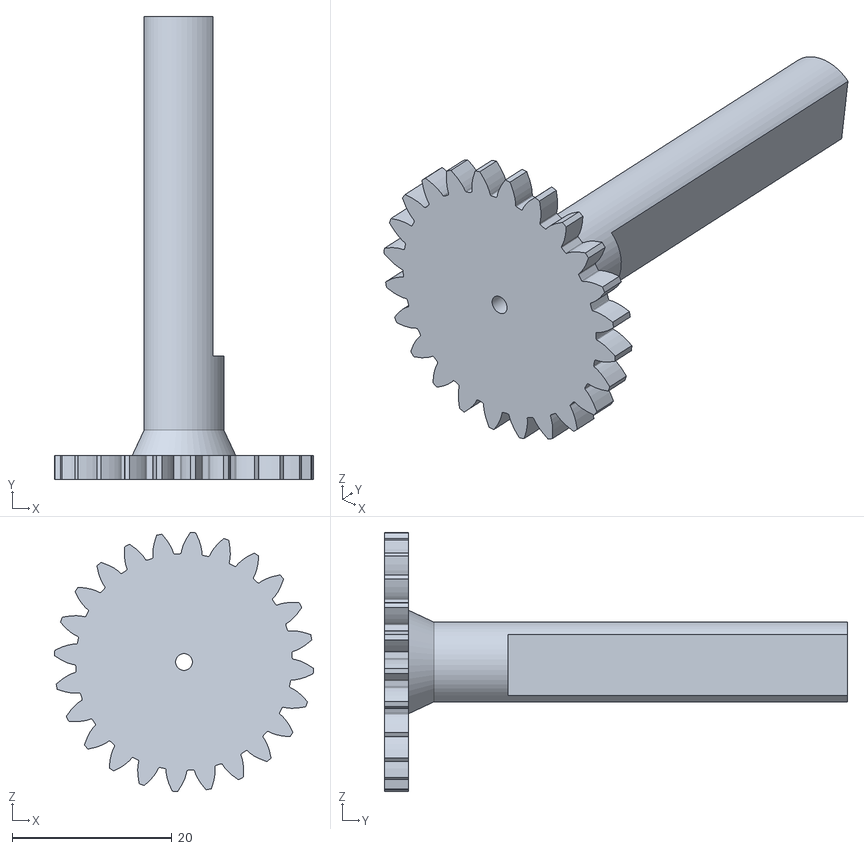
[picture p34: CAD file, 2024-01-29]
3D_models/iteration3/gearbox/output gear.stl
32.5 x 58.0 x 32.5

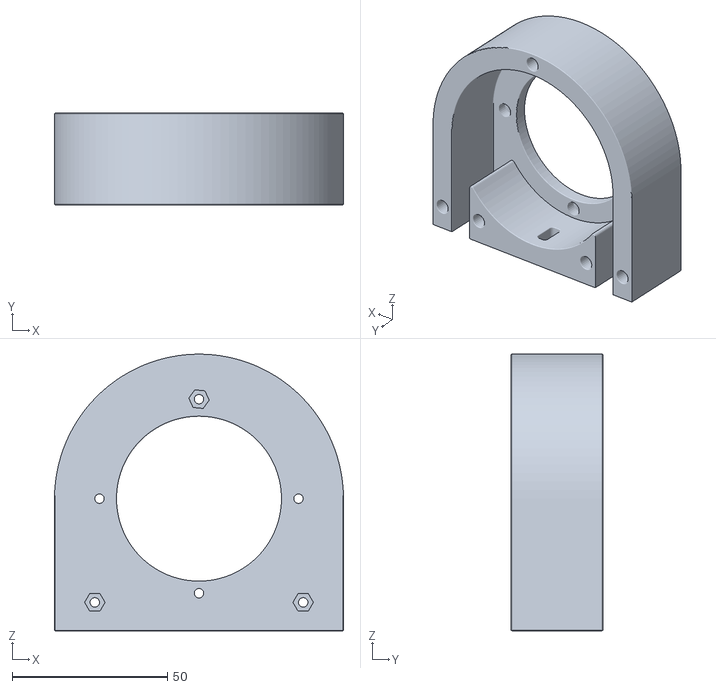
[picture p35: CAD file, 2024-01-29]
3D_models/iteration3/Housing.stl
93.2 x 29.6 x 89.2

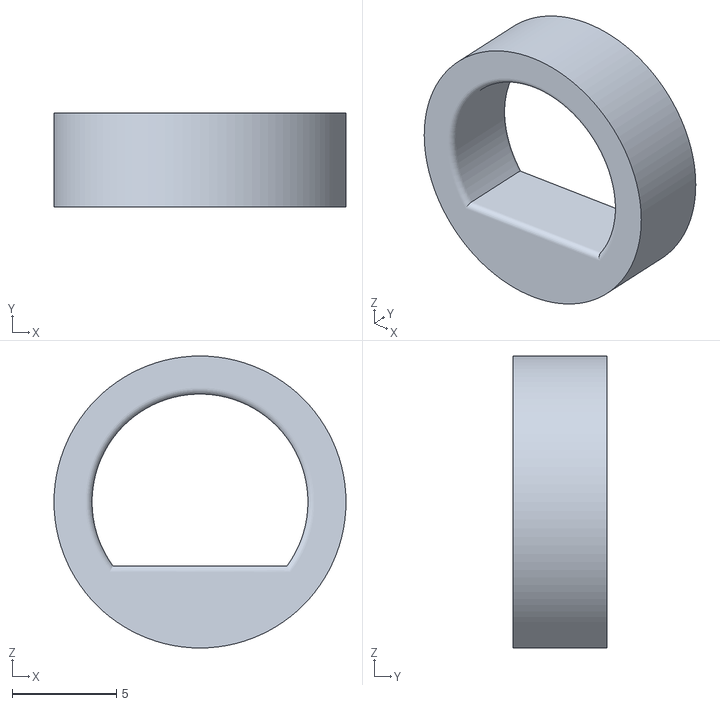
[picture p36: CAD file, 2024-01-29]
3D_models/iteration3/test/rotorShaftAdapter.stl
14.0 x 4.50 x 14.0

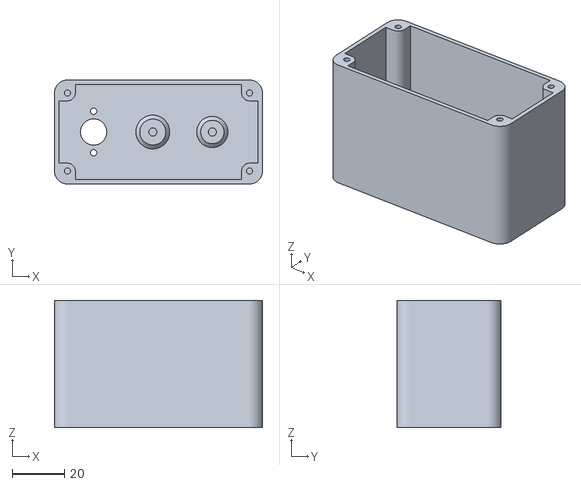
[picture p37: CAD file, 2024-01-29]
3D_models/iteration3/gearbox/box.stl
80.0 x 40.0 x 49.0

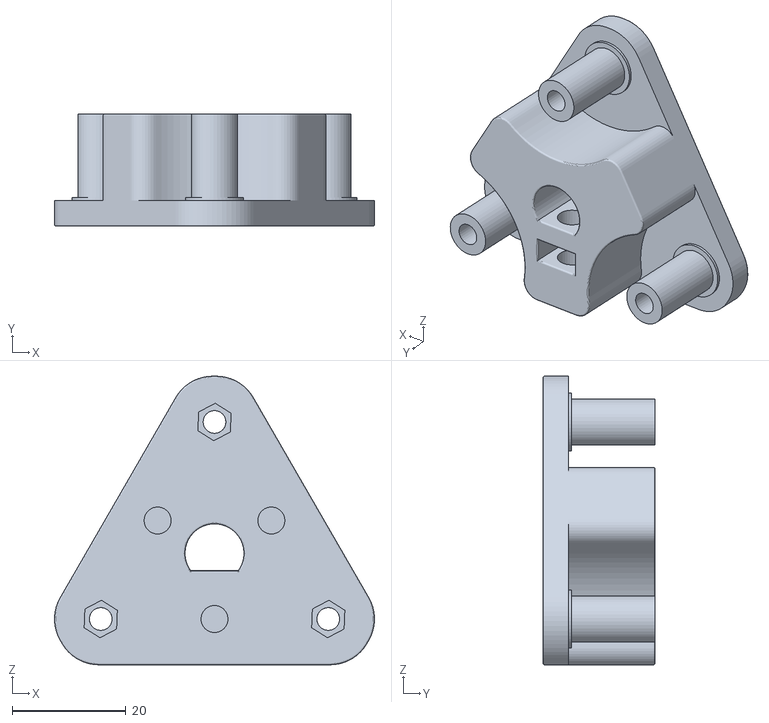
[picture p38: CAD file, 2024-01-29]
3D_models/iteration3/RotorBottom.stl
56.3 x 19.8 x 50.8

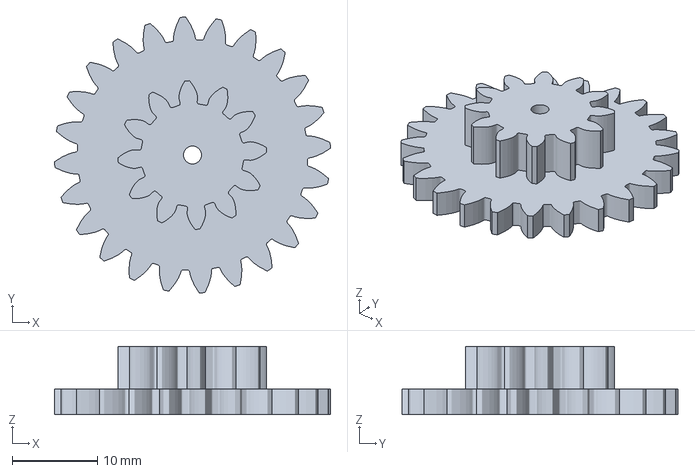
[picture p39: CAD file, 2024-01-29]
3D_models/iteration3/gearbox/gears.3mf
32.5 x 32.5 x 8.00 mm

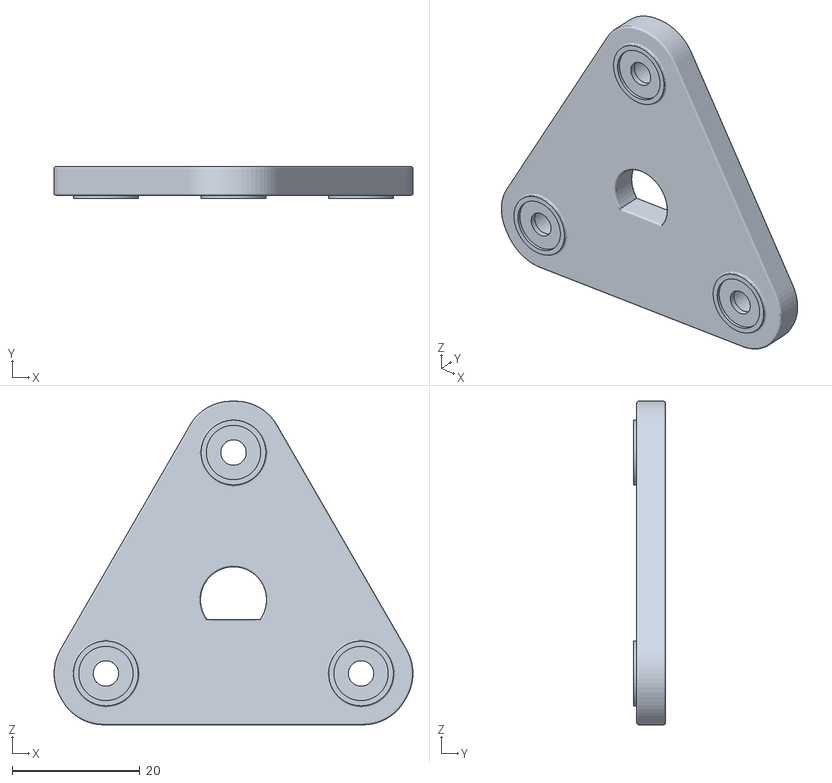
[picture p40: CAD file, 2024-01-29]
3D_models/iteration3/RotorTop.stl
56.3 x 5.00 x 50.8

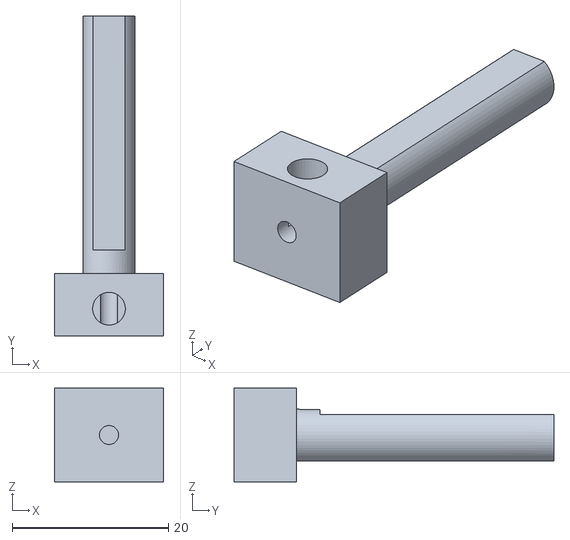
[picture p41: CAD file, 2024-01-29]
3D_models/iteration3/Coupler.stl
14.0 x 41.0 x 12.0

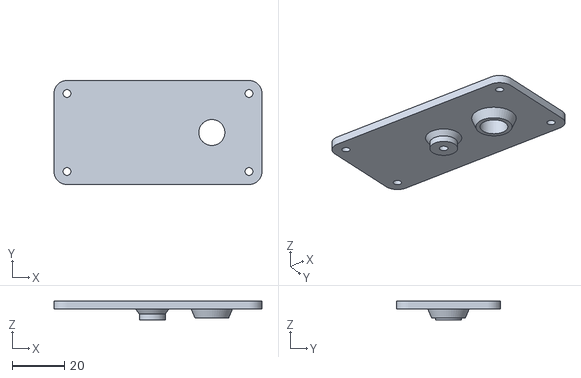
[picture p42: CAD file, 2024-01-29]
3D_models/iteration3/gearbox/lid.stl
80.0 x 40.0 x 7.30

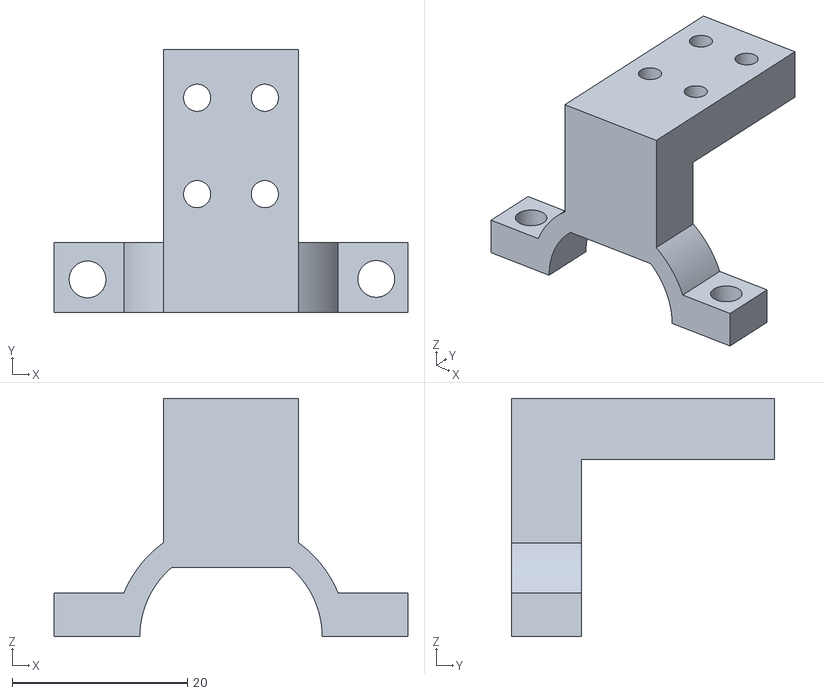
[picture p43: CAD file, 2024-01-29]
3D_models/iteration3/gearbox/motor mount.stl
40.4 x 30.0 x 27.2

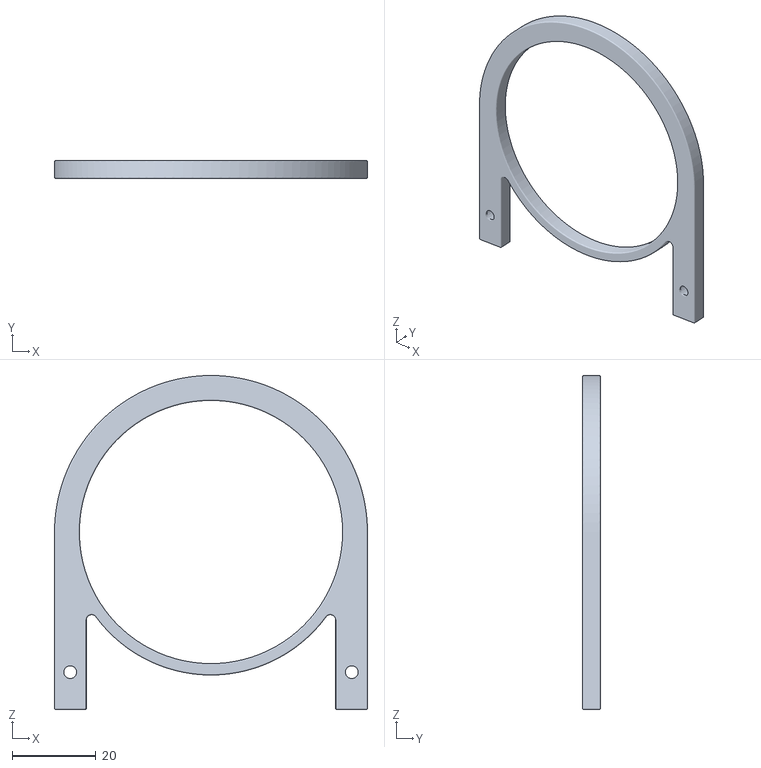
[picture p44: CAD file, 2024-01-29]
3D_models/iteration3/HoseSpacer.stl
74.7 x 4.25 x 79.7

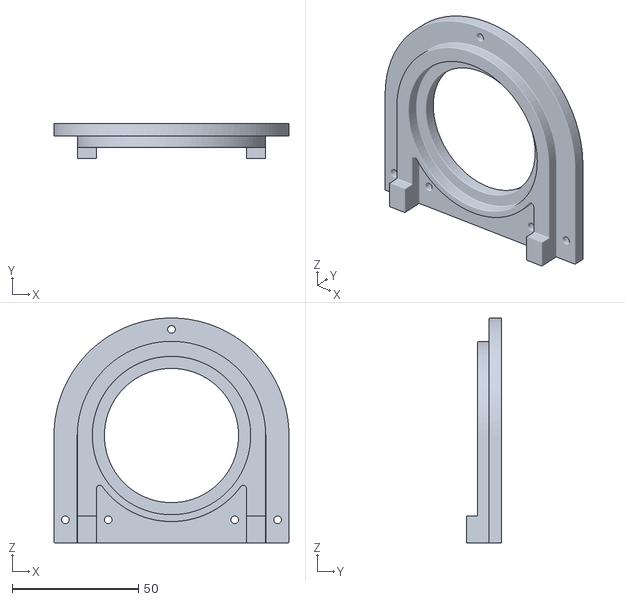
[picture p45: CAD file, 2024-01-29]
3D_models/iteration3/Lid.stl
93.2 x 14.0 x 89.2

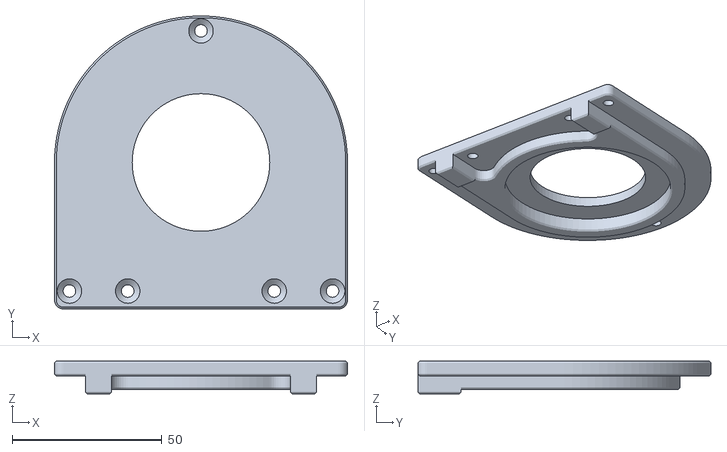
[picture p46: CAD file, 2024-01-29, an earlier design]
3D_models/iteration1/Cover.stl
98.0 x 98.0 x 11.0

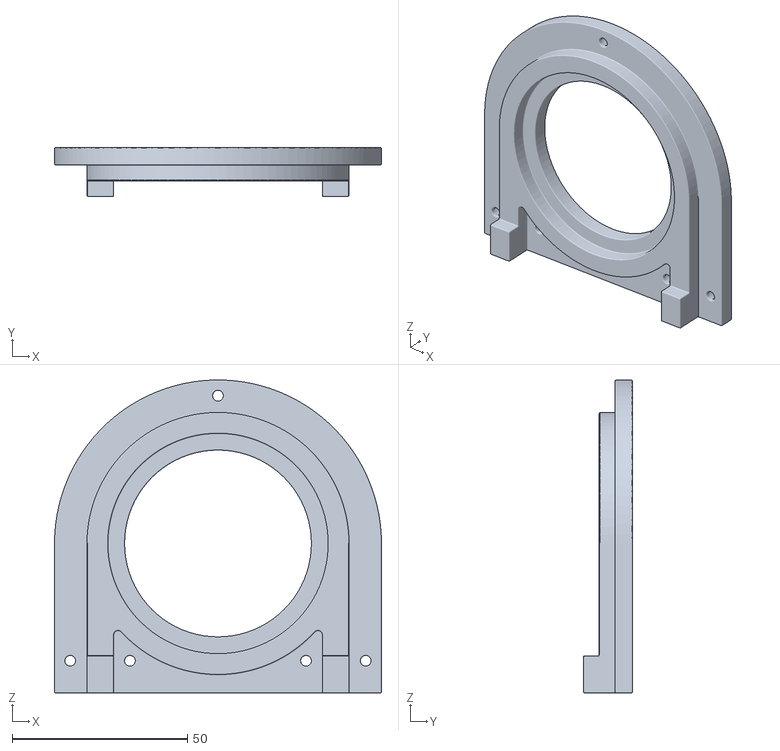
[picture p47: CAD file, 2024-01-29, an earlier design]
3D_models/Iteration2/Lid.stl
93.2 x 14.0 x 89.2

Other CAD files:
3D_models/iteration1/Housing.stl
3D_models/Iteration2/RotorBottom.stl
3D_models/iteration1/HoseSpacer.stl
3D_models/Iteration2/Housing.stl
3D_models/Iteration2/HoseSpacer.stl
3D_models/Iteration2/Housing_fix.stl
3D_models/Iteration2/RotorTop.stl
3D_models/Iteration2/nemaStem.stl
3D_models/iteration1/NemaAdapter.stl
3D_models/iteration1/Rotor.stl
3D_models/iteration1/RotorCover.stl
3D_models/iteration3/gearbox/gears.stl

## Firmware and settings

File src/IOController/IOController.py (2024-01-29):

from LiquidPump import LiquidPump
from pyrebase import initialize_app as initApp
from MocktenderConfig import MocktenderConfig
from pyrebase.pyrebase import Database
from functools import partial
from time import sleep
from sys import argv
import digitalio
import board
import asyncio
import adafruit_character_lcd.character_lcd as characterlcd

'''
This file implements the liquid pump subsystem of the Mocktender.
The recipe of a Mocktender in the Firebase DB is streamed asynchronously
to be able to capture all possible updates to the recipe.

Once a new recipe is received from the frontend, the IOController
will display on the LCD that it is dispensing liquid and will activate
the pump motors to do so.

While pumping, the IOController will prevent the frontend from making
any changes to the recipe by setting a "dispensing" flag in the
DB to true

Authors: 
>>> Ethan Bradley, 101158848
>>> Matt Reid, 101140593
'''
# Configuration details
FIREBASE_MOTOR_NAMES: list[str] = "l1,l2,l3".split(",")
MOCKTENDER_CONFIG = MocktenderConfig()
CONFIG_PROD = MocktenderConfig.CONFIG_PROD
CONFIG_DEV = MocktenderConfig.CONFIG_DEV

# --- Keywords used in the firebase real time database ---

# Recipe related keywords
ACK = "ack"
READY = "ready"
RECIPE = "recipe"
DISPENSING = "dispensing"

# Liquid level keywords
LIQUID1_DATASET = "LiquidLevel1"
LIQUID2_DATASET = "LiquidLevel2"
LIQUID3_DATASET = "LiquidLevel3"

# Pumping wait times
WAIT = 0.1
FEEDBACK_POUR = 5
FEEDBACK_WAIT = 5

# LCD is 16 columns by 2 rows
lcd_columns = 16
lcd_rows = 2

# Declare the pins used for the LCD
lcd_rs = digitalio.DigitalInOut(board.D23)
lcd_en = digitalio.DigitalInOut(board.D18)
lcd_d4 = digitalio.DigitalInOut(board.D22)
lcd_d5 = digitalio.DigitalInOut(board.D17)
lcd_d6 = digitalio.DigitalInOut(board.D27)
lcd_d7 = digitalio.DigitalInOut(board.D4)

# Initialise the lcd class
lcd = characterlcd.Character_LCD_Mono(lcd_rs, lcd_en, lcd_d4, lcd_d5, lcd_d6,
                                    lcd_d7, lcd_columns, lcd_rows)

def validateNodeFormat(data: dict):
    '''
    Verifies that the database query response provides
    an accurate format for the data.

    data requires the following keys:
    >>> data = {"ack", "ready", "drinkSize", "drinkPercentages"}

    the drinkPercentages key needs to have the following structure
    >>> drinkPercentages = {"l1", "l2", "l3"}
    '''
    recipeKeys = "ack,ready,drinkSize,drinkPercentages".split(",")
    hasAllRecipeKeys = all(x in data for x in recipeKeys)
    
    percentKeys = FIREBASE_MOTOR_NAMES.copy()
    percentages = data.get("drinkPercentages")

    if percentages is None:
        return False
    
    hasAllPercentKeys = all(x in percentages for x in percentKeys)
    
    return hasAllPercentKeys and hasAllRecipeKeys

def validateTimingFormat(pumpTiming: dict[str, float]) -> bool:
    '''
    Verify that the recipe pump timings are correct
    pumpTiming requires the following keys:
    >>> pumpTiming = {"l1", "l2", "l3"}
    '''
    return all(mName in pumpTiming.keys() for mName in FIREBASE_MOTOR_NAMES)


def acknowledgeRecipe(node: Database):
    ''' 
    Sets the "ack" flag in the firebase recipe
    to true
    '''
    node.child(RECIPE).child(ACK).set(True)

def lockDispenser(node: Database):
    ''' 
    Sets the "dispensing" flag in the firebase mocktender
    to true
    '''
    node.child(DISPENSING).set(True)

def unlockDispensing(node: Database):
    ''' 
    Sets the "dispensing" flag in the firebase mocktender
    to false
    '''
    node.child(DISPENSING).set(False)

def getLiquidLevels(node: Database):
    '''
    Gets the most recent liquid levels of each liquid as provided
    by the Firebase real time database
    '''
    ID = MOCKTENDER_CONFIG.getId()
    level1 = node.child(ID).child(LIQUID1_DATASET).order_by_key().limit_to_last(1).get().val()
    level2 = node.child(ID).child(LIQUID2_DATASET).order_by_key().limit_to_last(1).get().val()
    level3 = node.child(ID).child(LIQUID3_DATASET).order_by_key().limit_to_last(1).get().val()
    return [list(level.values()).pop() for level in (level1, level2, level3)]



def drinkMaker(message, motors: dict[str, LiquidPump], database: Database):
    '''
    Streams the recipe node of the Mocktender Firebase Real-time database.
    
    If the machine has not been locked and / or there is a new recipe,
    this function will actuate the liquid pumps, initially for a calculated
    amount of time based on the total liquid volume and the percentage
    of a liquid.

    After, queries will be made to the Firebase RTDB to check how much
    liquid has been pumped, and pumping will continue until a threshold
    volume is reached.
    '''
    ID = MOCKTENDER_CONFIG.getId()
    data = dict(database.child(ID).child(RECIPE).get().val())

    # check for new recipe or if machine is locked
    if data.get(ACK) or not data.get(READY):
        return

    # check that data format is correct
    if not validateNodeFormat(dict(data)):
        return
    
    pumpTiming: dict[str, float] = LiquidPump.validateRecipe(data)
    pumpVolumes: list[float] = [LiquidPump.convertSecondsToVolume(timing) 
        for timing in pumpTiming.values()]

    # check that timing format is correct
    if not validateTimingFormat(pumpTiming):
        return
    
    print(pumpTiming)
    acknowledgeRecipe(database.child(ID))
    print(f"Entered critical section.")

    # block other accounts from using the machine
    lockDispenser(database.child(ID))

    initialLiquidLevels = getLiquidLevels(database)
    
    lcd.message = "Dispensing\nDrink!"
    # Begin initial liquid dispensing using the motors
    for m, pTime in pumpTiming.items():
        motors[m].pour(pTime)

    # Wait for the motors to stop
    while any(motors[m].is_active for m in FIREBASE_MOTOR_NAMES):
        sleep(WAIT)

    temp_thresholds = [initialLiquidLevels[i] - pumpVolumes[i] 
                       for i in range(len(FIREBASE_MOTOR_NAMES))]
    # The threshold volume required to stop pumping
    thresholdLevels = {FIREBASE_MOTOR_NAMES[i]: temp_thresholds[i] 
                       for i in range(len(FIREBASE_MOTOR_NAMES))}
    # The liquid levels that have passed the threshold volume                   
    belowThreshold = {FIREBASE_MOTOR_NAMES[i]: False 
                      for i in range(len(FIREBASE_MOTOR_NAMES))}

    # feedback loop for more accurate pumping
    while any(not belowThreshold[m] for m in FIREBASE_MOTOR_NAMES):
        temp = getLiquidLevels(database)
        currentLevels = {FIREBASE_MOTOR_NAMES[i]: temp[i] for i in range(len(temp))}
        for m in FIREBASE_MOTOR_NAMES:
            if currentLevels.get(m) > thresholdLevels.get(m):
                motors[m].pour(FEEDBACK_POUR)
            else: # motor m will stop pumping
                belowThreshold.update({m: True})
            
        while any(motors[m].is_active for m in pumpTiming.keys()):
            sleep(FEEDBACK_WAIT)
        

    
    print("Pumping complete. Releasing critical section.")
    lcd.message = "Mocktender\nReady"
        
    # unblock other accounts from using the machine
    unlockDispensing(database.child(ID))
    
async def loop(motors: dict[str, LiquidPump], database: Database):    
    makeDrinkBind = partial(drinkMaker, motors = motors, database = database)
    while True:
        
        makeDrink = database.child(MOCKTENDER_CONFIG.getId()).child(
            RECIPE).stream(makeDrinkBind, is_async=True)
        try:
            await asyncio.wait([makeDrink], timeout=30)
        except asyncio.TimeoutError:
            print("loop @ ln65: Timed out")  
            


def main(PROD: bool):
    '''
    Pick the deployment environment to use for the device.
    Connects to the RTDB and begins the async loop
    for streaming recipes.
    '''
    CONFIG = CONFIG_PROD if PROD else CONFIG_DEV
    PINS = MOCKTENDER_CONFIG.getPins()

    motorVals = LiquidPump(forward=PINS[0]), LiquidPump(
        forward=PINS[1]), LiquidPump(forward=PINS[2])
    motorKeys = FIREBASE_MOTOR_NAMES.copy()

    MOTORS = dict(zip(motorKeys, motorVals))

    firebase = initApp(CONFIG)
    db = firebase.database()

    lcd.message = "Mocktender\nReady"

    asyncio.run(loop(MOTORS, db))
    
    
if __name__ == "__main__":
    main(True if len(argv) > 1 else False)

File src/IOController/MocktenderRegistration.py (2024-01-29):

from pyrebase import initialize_app as initApp
from SystemSimulator.MocktenderConfig import MocktenderConfig
from sys import argv
'''
The purpose of this file is to create a new Firebase Real-Time Database
schema for a Mocktender that is running for the first time.

Author: Ethan Bradley, 101158848
'''


def registerMocktender(PROD):
    '''
    Creates a new tree in the Firebase RTDB that matches the exact
    format required for this project under the devices ID name
    '''
    MOCK = MocktenderConfig()

    ID = MOCK.getId()
    STRUCTURE = MOCK.getStructure()

    # select production or development environment
    fbConfig = MOCK.CONFIG_PROD if PROD else MOCK.CONFIG_DEV

    db = initApp(fbConfig).database()
    db.child(ID).set(STRUCTURE)


if __name__ == "__main__":
    registerMocktender(True if len(argv) > 1 else False)

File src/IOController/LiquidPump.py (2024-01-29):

from gpiozero import DigitalOutputDevice

'''
This class is meant to control the rate at which the pump
pumps liquid at as well as calculate how long to pump liquid
for based on the size of a drink, the percentage of a liquid
of the drink, and the known flow rate of the pump

Author: Ethan Bradley, 101158848
'''

FLOW_RATE = 100  # mL per minute
DRINK_SIZE = "drinkSize"
DRINK_PERCENTAGES = "drinkPercentages"

DRINK_PERCENTAGE_MAX = 100
DRINK_PERCENTAGE_MIN = 0
DRINK_SIZE_MIN = 0

SIG_FIGS = 3  # number of figures to round to

ML_CONVERSION = 100  # conversion factor for milliliters

class LiquidPump(DigitalOutputDevice):
    def __init__(self, forward, active_high=True, initial_value=False, pin_factory=None):
        super().__init__(pin=forward, active_high=active_high,
                         initial_value=initial_value, pin_factory=pin_factory)

    def pour(self, seconds: float):
        self.blink(seconds, 1, n=1, background=True)

    @classmethod
    def convertPercentToSeconds(self, liquidPercentage,
                                totalVolume) -> float:
        '''
        Converts the percentage of the liquid in the drink to the volume of
        that liquid using the totalVolume as a reference. Using that volume,
        the known flow rate of the pump will be used to convert it to the
        number of seconds required to pump.

        Returns -1 if the percentage of the liquid is less than 0 or greater
        than 100
        '''
        if (DRINK_PERCENTAGE_MIN > liquidPercentage > DRINK_PERCENTAGE_MIN):
            return -1

        liquidVolume = (liquidPercentage / ML_CONVERSION) * totalVolume  # mL
        numPumpSeconds = (liquidVolume / FLOW_RATE) * 60

        return round(numPumpSeconds, SIG_FIGS)

    @classmethod
    def convertSecondsToVolume(self, pumpSeconds) -> float:
        return (pumpSeconds / 60) * FLOW_RATE
		
    @classmethod
    def validateRecipe(self, recipe: dict) -> dict[str, float]:
        '''
        Takes in a recipe from the backend server and converts it to the
        amount of time that the pumps would need to run to create the
        recipe.
        If the recipe is invalid (None values, sum(percentages) > 100,
        negative percentages) the method should return a tuple containing None.

        Example 1 (no issues):
        >>> recipe = {DRINK_SIZE: 15, DRINK_PERCENTAGES: [25, 25, 50]}
        >>> actualResult = LiquidPump.validateRecipe(recipe)
        >>> expectedResult = (0.062, 0.062, 0.125)
        >>> print(compare(actualResult, expectedResult)) # true

        Example 2 (negative size and percentage, sum(percentages) > 100):
        >>> recipe = {DRINK_SIZE: -25, DRINK_PERCENTAGES: [25, 150, -50]}
        >>> actualResult = LiquidPump.validateRecipe(recipe)
        >>> expectedResult = (None,)
        >>> print(compare(actualResult, expectedResult)) # true
        '''

        INVALID_RECIPE = {"l1": None}

        # recipe and recipe members are None
        if (recipe is None):
            return INVALID_RECIPE
        if (recipe[DRINK_SIZE] is None or recipe[DRINK_PERCENTAGES] is None):
            return INVALID_RECIPE

        percentagesDict: dict = recipe.get(DRINK_PERCENTAGES)
        percentages = list(percentagesDict.values())
        drinkSize = recipe[DRINK_SIZE]

        # drinkSize is negative
        if (drinkSize <= DRINK_SIZE_MIN):
            return INVALID_RECIPE
        # Percentages are negative
        if any(percent < DRINK_PERCENTAGE_MIN for percent in percentages):
            return INVALID_RECIPE
        # Percentages sum to over 100%
        if sum(percentages) > DRINK_PERCENTAGE_MAX:
            return INVALID_RECIPE

        actuators = "l1,l2,l3".split(",")
        actuatorTimeMap = {}
        for percent in percentages:
            actuatorTimeMap[actuators.pop(0)] = self.convertPercentToSeconds(percent, drinkSize)

        return actuatorTimeMap

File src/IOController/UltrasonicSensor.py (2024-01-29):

"""
Ultrasonic sensor object used to interact with the ultrasonic sensor hardware
Gives the distance in cm when requested

Author: Matt Reid
"""
from gpiozero import DistanceSensor
import time

class UltrasonicSensor:
    def __init__(self, echo_pin, trigger_pin):
        """
        Function to initialize an ultrasonic sesnor for the 
        Mocktender. Takes the echo and trigger pins
        """
        self._sensor = DistanceSensor(echo=echo_pin, trigger=trigger_pin)

    def get_distance(self):
        """
        Function to get the distance from the ultrasonic
        sensor.
        """

        return self._sensor.distance * 100 + 1.5
        
    
